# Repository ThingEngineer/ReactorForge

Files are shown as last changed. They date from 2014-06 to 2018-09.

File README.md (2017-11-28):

ReactorForge - They catalyst for creation
============

This repository contains hardware designs, board schematics, firmware, and software for ReactorForge, an open source high power induction heater platform.

Updates, polls, etc. on this project are being posted on the new Patreon page: [ReactorForge on Patreon](https://www.patreon.com/ReactorForge). You can also support the future of this project there as well.

For project status, official blog, and information about hardware availability visit [ReactorForge.com](https://reactorforge.com/) and be sure to read the [ReactorForge Wiki](https://github.com/joshcam/ReactorForge/wiki).

ReactorForge Control Board - ReactorCore
(photo: assembly of the beta ReactorCore, ReactorForge CriticalMass control board)

principal author: Joshua Campbell josh.lee.campbell@gmail.com

## Project Description
The ReactorForge project is an open source hardware platform for high power induction heating, designed for heavy use and reliable performance in real world applications.

Using fewer discreet components than most commercial induction heaters, the ReactorForge has less failure points and is easy to assemble. It is an open source project with all plans, schematics and code available under the creative commons BY-SA 4.0 license. This not only benefits the maker community and improves future designs but also makes self repair a possibility for those who have purchased kits, rather than relying on expensive factory repairs to proprietary commercial units.

The ReactorForge will be made available in a raw kit form and an ARU (Almost Ready to Use) kit that can be assembled in just a couple hours. Learn about high power electronics while building an awesome machine. The same systems in an induction heater also drive many of todays modern advances such as electric vehicles, renewable energy power inverters, cutting edge research equipment, and much more. Whether your goals are academic or you want to start using an induction heater today the ReactorForge project brings that within reach.

The ReactorForge costs thousands less than equivalent commercial models with features that are not available anywhere else. It has an easy one button/pedal interface for those that want simple to use set and forget type operation. But for those that want full control there are powerful features that let you monitor and regulate operation based on virtually any parameter. And since the entire platform is open source you have a head start to hacking the core (main control board).

CriticalMass Test Run (http://www.youtube.com/watch?v=C8s0zIcqVfk)

(video: Test run of the ReactorForge : CriticalMass +15Kw platform)

## Safety Notice and Disclaimer
An induction heater is a high power device that should be treated with hazards similar but not limited to that of induction cooktops and welders. In addition to that, the following safety guidelines should be observed:

* Don't wear metal jewelry, especially rings near the work coil. Heating can occur a few inches from the coil depending on its geometry.
* Be cautious if you have metal implants, they too could heat up if held near the work coil.
* If you have a pacemaker or other medical implants never use or be near this machine while it is in operation.
* Keep electronics at least 12 inches from the work coil while in operation to avoid damage to these devices.
* Never touch the work coil. Although it is isolated from dangerous mains current, there is still high power present. Holding metal objects that touch or short out the work coil will not harm the unit.
* Wear appropriate PPE, including but not limited to safety glasses and gloves.

We hold no responsibility or liability for injury to person or damage to property should you choose to build and operate one of these machines. If you feel you are not qualified to build or operate an induction heater find someone qualified and willing to assist you.

## Open Source
  <br />This work is licensed under a <a rel="license" href="http://creativecommons.org/licenses/by-sa/4.0/">Creative Commons Attribution-ShareAlike 4.0 International License</a>.

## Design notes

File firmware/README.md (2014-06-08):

ReactorForge Core (the main controller board) firmware is written in C. The projects presented here will use AVR Studio 6. 

Firmware can be updated with an ICSP programer via the on board programing header or by putting the unit in DFU (Device Firmware Update) mode and uploading the new firmware image over a serial connection.

Some older revisions were written in basic using the MCS Electronics BASCOM-AVR compiler, those versions are not supported or active.

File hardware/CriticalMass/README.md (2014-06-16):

ReactorForge - CriticalMass
============

CriticalMass is the general purpose base unit. Built to run on 240V single phase and be usable on a practical level with large work pieces.

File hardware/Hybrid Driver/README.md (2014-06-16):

ReactorForge - Hybrid Driver
============

This directory contains the schematic and board file for Hybrid Driver, a dual IGBT module gate driver based on the Powerex M57962L hybrid IC.

See the Wiki for [Documentation](https://github.com/joshcam/ReactorForge/wiki/ReactorForge-Hybrid-Driver)

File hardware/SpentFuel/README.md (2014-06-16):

ReactorForge - SpentFuel
============

SpentFuel is where the older prototypes that have provided a foundation for other models, learning experice and or headaches are stored. Proceed with caution!

Schematic and board designs are in CadSoft EAGLE PCB Design Software.

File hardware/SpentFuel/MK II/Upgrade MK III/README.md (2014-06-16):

MKIII - Core Upgrade
============

This was an upgrade to the prototype (MKII) using the old tank voltage feedback, PLL style control with gate drive transformer driven IGBTs. The upgrade (an early version ultimately meant to control the MKIII model) allowed the unit to run on inverter current feedback with no PLL (all digital phase control performed by the microcontroller) and make use of the new hybrid ic driver with over current protection.

The original source files for this quick upgrade were mistakenly overwritten when work on the actual Core began, all that remained was a mostly complete image export.

**Bare MKIII Control Board**

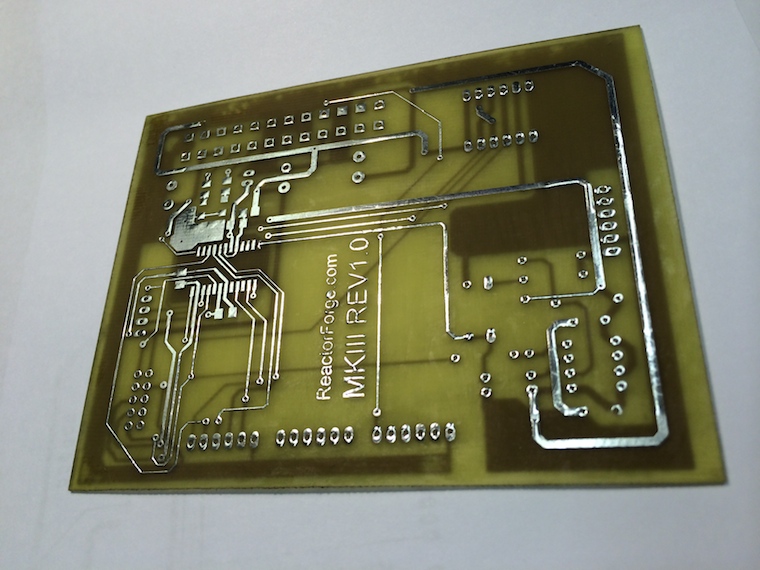
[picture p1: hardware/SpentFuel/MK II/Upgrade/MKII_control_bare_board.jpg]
Bare MKIII Control Board


**Populated MKIII Control Board**

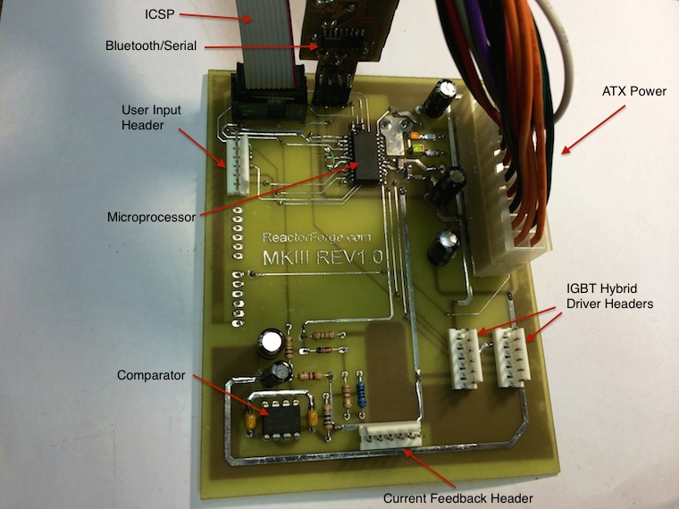
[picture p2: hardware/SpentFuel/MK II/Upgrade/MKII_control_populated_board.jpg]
Populated MKIII Control Board


**Test Run**

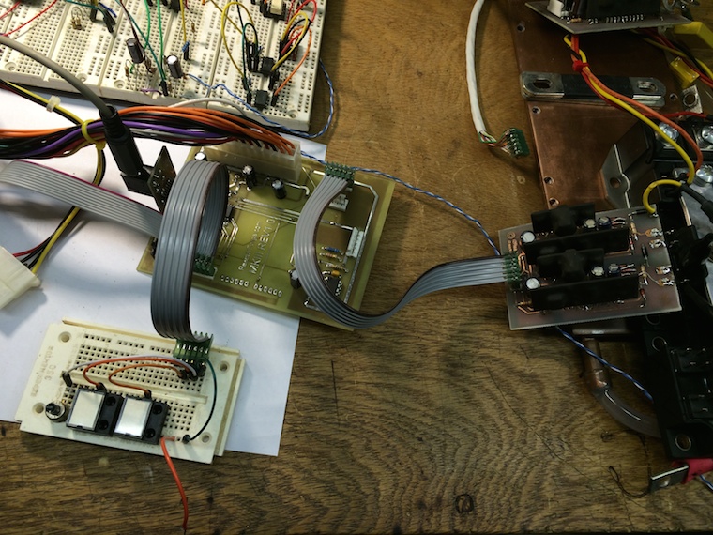
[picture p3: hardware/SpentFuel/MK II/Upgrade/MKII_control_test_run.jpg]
Test Run


**Ready To Go**

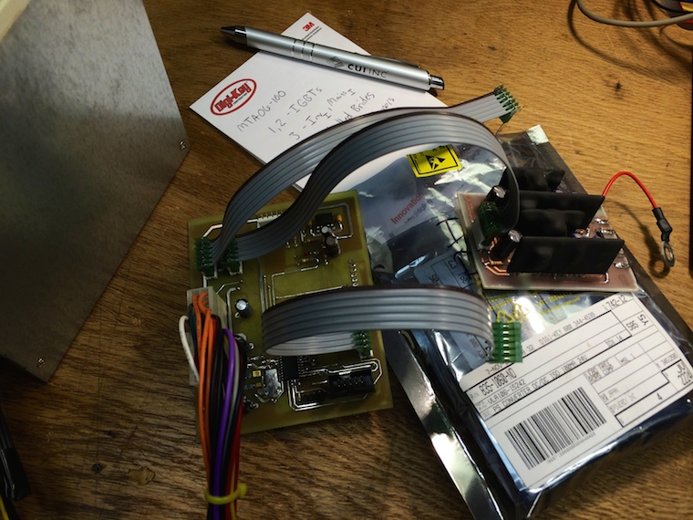
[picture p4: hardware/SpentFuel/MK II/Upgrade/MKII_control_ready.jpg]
Ready To Go


**Old MKII Board Under New MKIII Control Board**

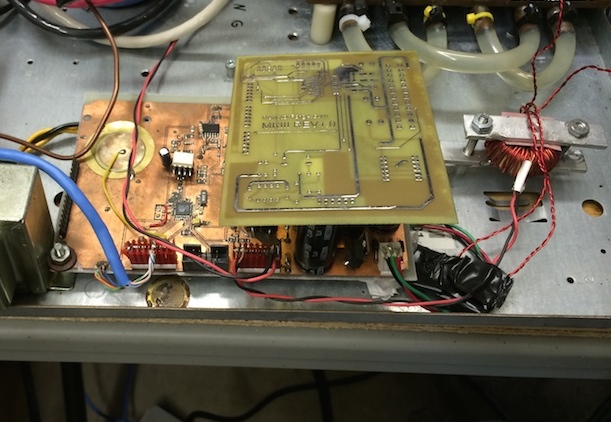
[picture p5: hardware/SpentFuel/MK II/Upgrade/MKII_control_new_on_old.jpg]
Old MKII Board Under New MKIII Control Board


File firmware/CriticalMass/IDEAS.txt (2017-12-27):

****IDEA Scratchpad****

Use a boot loader
	One port to program and monitor serial data
  Additional programmer not needed
	Will have to add a usb to serial chip and passives to main board
  Will make firmware updates / hacking easier for end user

Use an LCD with as serial backpack (i2s, spi, etc)
  Current LCD configuration uses 6 ports
  Will free up ports using a common bus
  Don't currently need the ports but its something to consider
	Simpler programing interface with standard libraries
  Slower refresh but that shouldn't matter

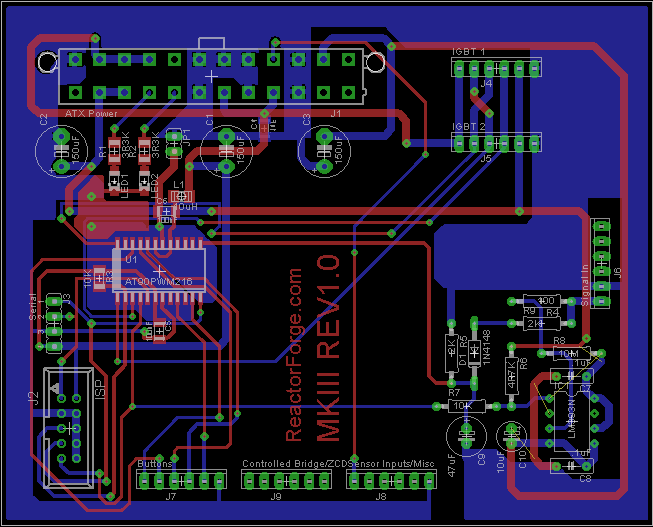
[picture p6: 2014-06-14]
hardware/SpentFuel/MK II/Upgrade MK III/MK_III_control_upgrade.png

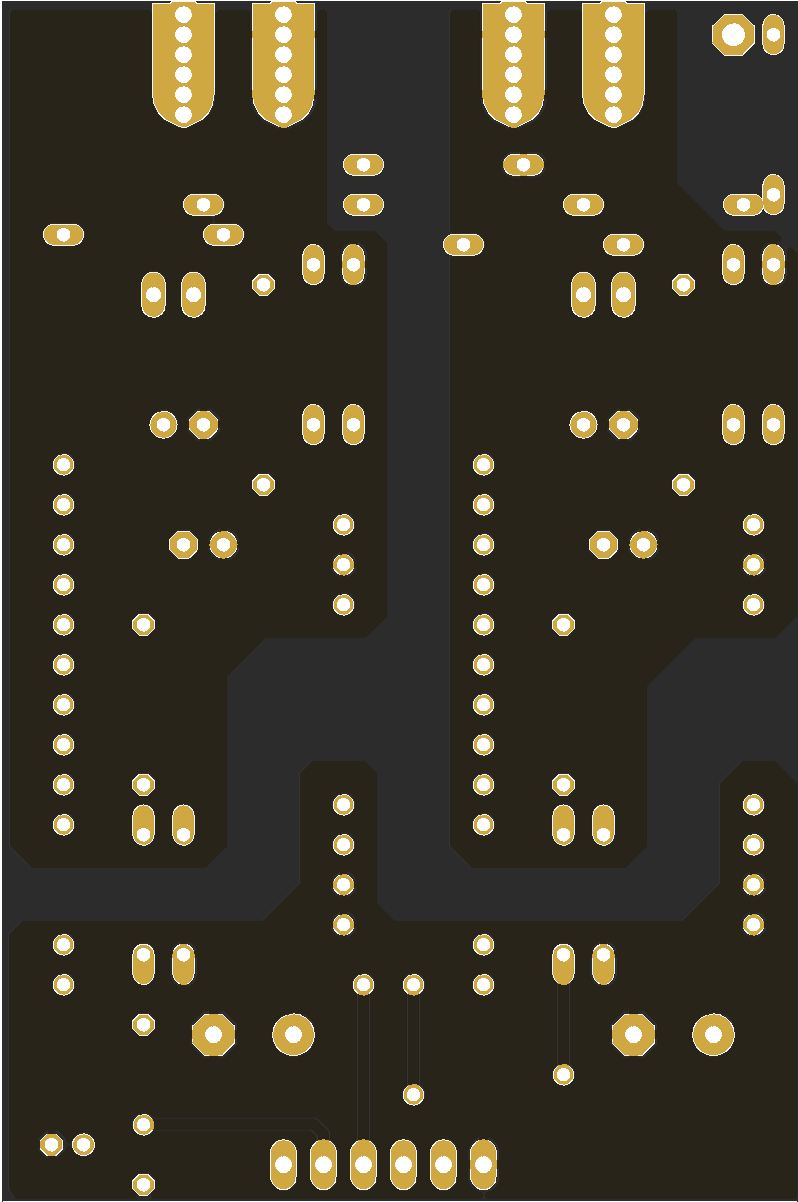
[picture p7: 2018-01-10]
hardware/Hybrid Driver/Hybrid Driver_Bottom.png

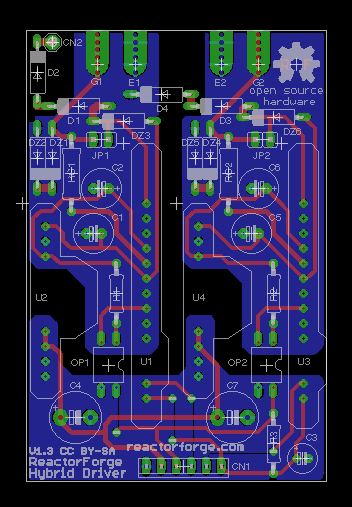
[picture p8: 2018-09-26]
hardware/Hybrid Driver/Hybrid Driver v1.3 Board.png

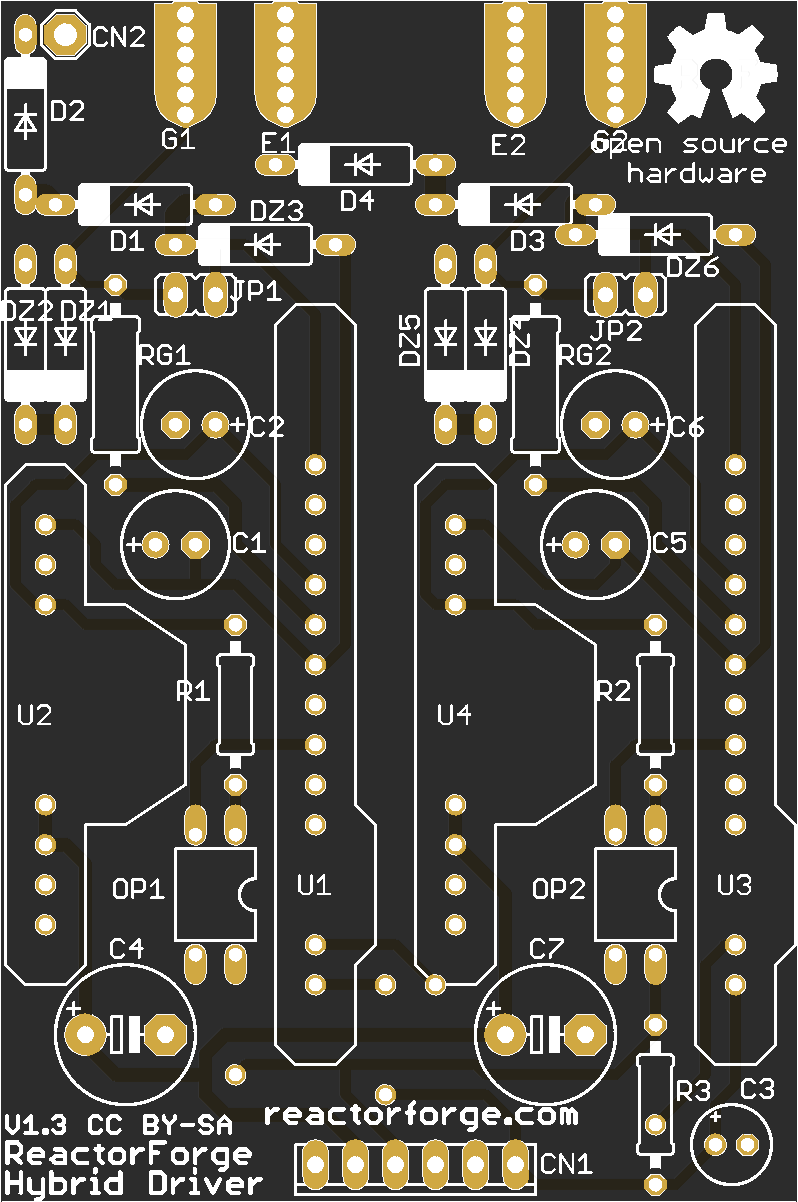
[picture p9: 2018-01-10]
hardware/Hybrid Driver/Hybrid Driver_Top.png

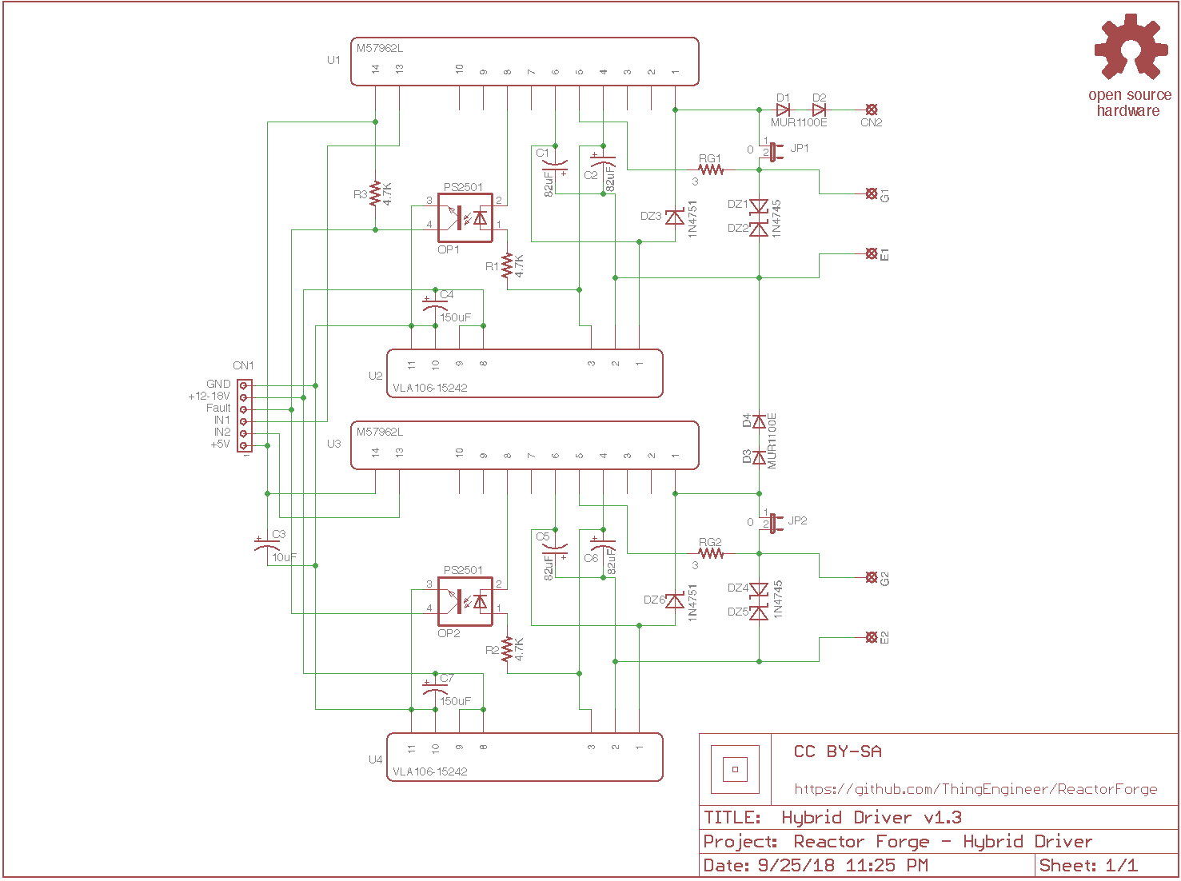
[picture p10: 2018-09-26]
hardware/Hybrid Driver/Hybrid Driver v1.3 Schematic.png

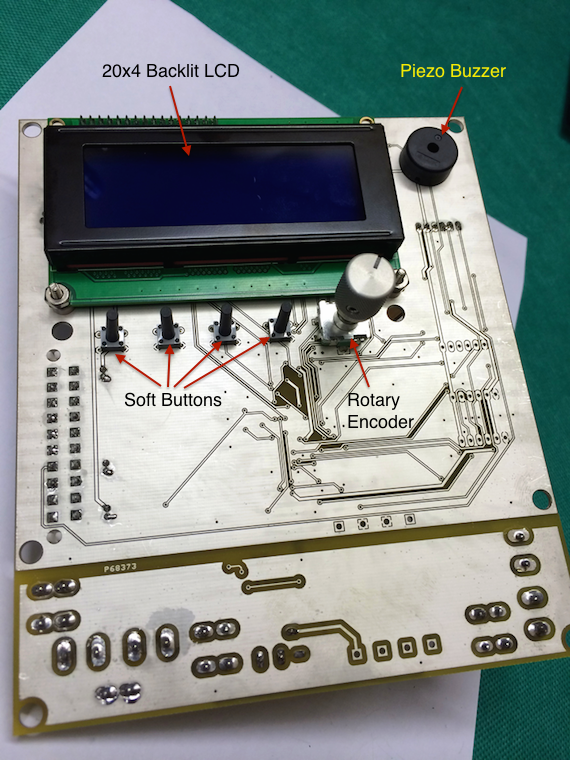
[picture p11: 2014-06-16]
doc/images/core/rf_core_front.png

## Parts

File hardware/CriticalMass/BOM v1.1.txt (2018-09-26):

Partlist exported from /Users/Josh/Dropbox/Projects/eagle/Induction Heaters/CriticalMass/Reactor Core.sch at 9/25/18 8:56 PM

Part  Value         Device                   Package                  Description                                       MF                        MPN                OC_FARNELL OC_NEWARK PN_DIGI-KEY          
C1    100uF         CPOL-USE2-5              E2-5                     POLARIZED CAPACITOR, American symbol                                                                                                     
C2    100uF         CPOL-USE2-5              E2-5                     POLARIZED CAPACITOR, American symbol                                                                                                     
C3    100uF         CPOL-USE2-5              E2-5                     POLARIZED CAPACITOR, American symbol                                                                                                     
C4    .01uF         C-USC1206                C1206                    CAPACITOR, American symbol                                                                                                               
C5    .1uF          C-USC1206K               C1206K                   CAPACITOR, American symbol                                                                                                               
C6    .1uF          C-USC1206K               C1206K                   CAPACITOR, American symbol                                                                                                               
C7    .1uF          C-USC1206                C1206                    CAPACITOR, American symbol                                                                                                               
C8    .1uF          C-USC1206                C1206                    CAPACITOR, American symbol                                                                                                               
C9    10uF          CPOL-US153CLV-0405       153CLV-0405              POLARIZED CAPACITOR, American symbol                                                                                                     
C10   .01uF         C-USC1206K               C1206K                   CAPACITOR, American symbol                                                                                                               
C11   .1uF          C-USC1206                C1206                    CAPACITOR, American symbol                                                                                                               
C12   .01uF         C-USC1206K               C1206K                   CAPACITOR, American symbol                                                                                                               
C13   .01uF         C-USC1206K               C1206K                   CAPACITOR, American symbol                                                                                                               
C14   10uF          CPOL-US153CLV-0405       153CLV-0405              POLARIZED CAPACITOR, American symbol                                                                                                     
C15   1000pF        C-USC1206                C1206                    CAPACITOR, American symbol                                                                                                               
C16   47uF          CPOL-US153CLV-0605       153CLV-0605              POLARIZED CAPACITOR, American symbol                                                                                                     
D1    NSR0340HT1G   NSR0340HT1G              SOD-323                  NSR0340HT1G                                                                                                                              
D2    1N4148        1N4148                   SOD-123                  1N4148                                                                                                                                   
D3    NSR0340HT1G   NSR0340HT1G              SOD-323                  NSR0340HT1G                                                                                                                              
D4    NSR0340HT1G   NSR0340HT1G              SOD-323                  NSR0340HT1G                                                                                                                              
D5    NSR0340HT1G   NSR0340HT1G              SOD-323                  NSR0340HT1G                                                                                                                              
D6    NSR0340HT1G   NSR0340HT1G              SOD-323                  NSR0340HT1G                                                                                                                              
D7    1N4148        1N4148                   SOD-123                  1N4148                                                                                                                                   
D8    1N4148        1N4148                   SOD-123                  1N4148                                                                                                                                   
D9    1N4148        1N4148                   SOD-123                  1N4148                                                                                                                                   
D10   1N4148        1N4148                   SOD-123                  1N4148                                                                                                                                   
D11   1N4148        1N4148                   SOD-123                  1N4148                                                                                                                                   
D16   5.1V          MM3Z5V1ST1G              SOD-323                  MM3Z5V1ST1G                                       5.1V 200MW                MM3Z5V1ST1G                             MM3Z5V1ST1GOSCT-ND   
F1    50mA Fast     TR5                      TR5                      FUSE                                              Bel Fuse Inc              MRF 50             unknown    unknown   507-1715-ND          
F2    1A Slow       FC211-5X20               FC211-5X20               FC 211                                                                                                                                   
F3    10A Slow      FC211-5X20               FC211-5X20               FC 211                                                                                                                                   
J1    ATX Power     5566-20                  5566-20                  Mini FIT connector 20 pol                                                   39-29-9206         unknown    unknown   2M3873-ND            
J2    ICSP          057-006-1                057-006-1                CONNECTOR                                                                                      unknown    unknown                        
J3    1286-ST       PIN262409-1              62409-1                  Flachstecker Typ Tyco/Electronics/AMP TAB, FASTON                                              unknown    unknown                        
J4    IGBT 1        MTA06-100                10X06MTA                 AMP connector                                                                                                                            
J5    IGBT 2        MTA06-100                10X06MTA                 AMP connector                                                                                                                            
J6    Signal In     MTA06-100                10X06MTA                 AMP connector                                                                                                                            
J7    I/O           MTA06-100                10X06MTA                 AMP connector                                                                                                                            
J8    1286-ST       PIN262409-1              62409-1                  Flachstecker Typ Tyco/Electronics/AMP TAB, FASTON                                              unknown    unknown                        
J9    1286-ST       PIN262409-1              62409-1                  Flachstecker Typ Tyco/Electronics/AMP TAB, FASTON                                              unknown    unknown                        
J10   Misc          MTA06-100                10X06MTA                 AMP connector                                                                                                                            
J11   1286-ST       PIN262409-1              62409-1                  Flachstecker Typ Tyco/Electronics/AMP TAB, FASTON                                              unknown    unknown                        
J12   1286-ST       PIN262409-1              62409-1                  Flachstecker Typ Tyco/Electronics/AMP TAB, FASTON                                              unknown    unknown                        
J13   1286-ST       PIN262409-1              62409-1                  Flachstecker Typ Tyco/Electronics/AMP TAB, FASTON                                              unknown    unknown                        
J14   1286-ST       PIN262409-1              62409-1                  Flachstecker Typ Tyco/Electronics/AMP TAB, FASTON                                              unknown    unknown                        
L1    10uH          L-USL3225P               L3225P                   INDUCTOR, American symbol                                                                                                                
L2    22uH          L-USL3225P               L3225P                   INDUCTOR, American symbol                                                                                                                
LCD1  J204A         J204A                    LCD-20X4                 J204A                                                                                                                                    
LED2                LEDCHIPLED_1206          CHIPLED_1206             LED                                                                                                                                      
LOGO1 LOGO_CC-BY-SA LOGO_CC-BY-SA            LOGO_CC-BY-SA                                                                                                                                                     
OK1   LTV816S       LTV816S                  SMD4                     OPTO COUPLER                                                                                   unknown    unknown                        
OK2   MOC3022S      MOC3022S                 6-SMD                    MOC3022S                                          Lite-On Inc               MOC3022S                                160-1377-5-ND        
OK3   MOC3022S      MOC3022S                 6-SMD                    MOC3022S                                          Lite-On Inc               MOC3022S                                160-1377-5-ND        
Q1    MMBT4401      MMBT4401                 SOT23                    MMBT4401                                                                                                                                 
Q2    MMBT4401      MMBT4401                 SOT23                    MMBT4401                                                                                                                                 
Q4    MMBT4401      MMBT4401                 SOT23                    MMBT4401                                                                                                                                 
R1    1K            R-US_R1206               R1206                    RESISTOR, American symbol                         Stackpole Electronics Inc RNCP1206FTD100R                         RNCP1206FTD100RCT-ND 
R2    220           R-US_R1206               R1206                    RESISTOR, American symbol                                                                                                                
R3    10K           R-US_R1206               R1206                    RESISTOR, American symbol                                                                                                                
R4    100           R-US_R1206               R1206                    RESISTOR, American symbol                                                                                                                
R5    4K7           R-US_R1206               R1206                    RESISTOR, American symbol                                                                                                                
R6    4K7           R-US_R1206               R1206                    RESISTOR, American symbol                                                                                                                
R7    10K           R-US_R1206               R1206                    RESISTOR, American symbol                                                                                                                
R8    10M           R-US_R1206               R1206                    RESISTOR, American symbol                                                                                                                
R9    100           R-US_R1206               R1206                    RESISTOR, American symbol                                                                                                                
R10   330           R-US_M1206               M1206                    RESISTOR, American symbol                                                                                                                
R12   330           R-US_R1206               R1206                    RESISTOR, American symbol                                                                                                                
R13   220K          R-US_R1206               R1206                    RESISTOR, American symbol                                                                                                                
R14   10K           R-US_R1206               R1206                    RESISTOR, American symbol                                                                                                                
R16   10K           TRIMMER_3314G            TRIMMER_3314G            3314G Trimmer Pot                                                                                                                        
R17   2k            R-US_R1206               R1206                    RESISTOR, American symbol                                                                                                                
R18   330R          R-US_R1206               R1206                    RESISTOR, American symbol                                                                                                                
R19   620R          R-US_R1206               R1206                    RESISTOR, American symbol                                                                                                                
R20   1K            R-US_R1206               R1206                    RESISTOR, American symbol                                                                                                                
R21   3K3           R-US_R1206               R1206                    RESISTOR, American symbol                                                                                                                
R22   1K            R-US_R1206               R1206                    RESISTOR, American symbol                                                                                                                
R23   100R          R-US_R1206               R1206                    RESISTOR, American symbol                                                                                                                
R24   4K7           R-US_R1206               R1206                    RESISTOR, American symbol                                                                                                                
R25   10K           R-US_M1206               M1206                    RESISTOR, American symbol                                                                                                                
R26   10K           R-US_M1206               M1206                    RESISTOR, American symbol                                                                                                                
R27   10K           R-US_R1206               R1206                    RESISTOR, American symbol                                                                                                                
R28   10K           R-US_R1206               R1206                    RESISTOR, American symbol                                                                                                                
R29   1K            R-US_R1206               R1206                    RESISTOR, American symbol                                                                                                                
R30   220K          R-US_R1206               R1206                    RESISTOR, American symbol                                                                                                                
R31   22K           R-US_R1206               R1206                    RESISTOR, American symbol                                                                                                                
R32   1K            R-US_R1206               R1206                    RESISTOR, American symbol                                                                                                                
R33   4K7           R-US_R1206               R1206                    RESISTOR, American symbol                                                                                                                
R34   100           R-US_R1206               R1206                    RESISTOR, American symbol                         Stackpole Electronics Inc RNCP1206FTD100R                         RNCP1206FTD100RCT-ND 
R35   24            R-US_R2512               R2512                    RESISTOR, American symbol                         TE Connectivity           352124RFT                               A115993CT-ND         
R36   330           R-US_R1206               R1206                    RESISTOR, American symbol                                                                                                                
R37   330           R-US_R1206               R1206                    RESISTOR, American symbol                                                                                                                
R38   2K            R-US_R1206               R1206                    RESISTOR, American symbol                         Stackpole Electronics Inc RNCP1206FTD100R                         RNCP1206FTD100RCT-ND 
R39   330           R-US_R1206               R1206                    RESISTOR, American symbol                                                                                                                
SG1   PS1740P02E    F/EE17P                  F/EE17P                  BUZZER Source: Buerklin                                                     PS1740P02E         unknown    unknown   445-2528-ND          
SJ1   0             SJ                       SJ                       SMD solder JUMPER                                                                                                                        
SJ2   0             SJ                       SJ                       SMD solder JUMPER                                                                                                                        
SW1   PEC11R_SW     PEC11R_SW                BOURNS_PEC11R_SW         Bourns Rotary Encoder PEC11R series with switch   Bourns                    PEC11R-4215K-S0012                      PEC11R-4215K-S0012-ND
SW2   FSM14JH       SW_TACTILE_TOP_ACTIVATED SW_TACTILE_TOP_ACTIVATED                                                                                                                                          
SW3   FSM14JH       SW_TACTILE_TOP_ACTIVATED SW_TACTILE_TOP_ACTIVATED                                                                                                                                          
SW4   FSM14JH       SW_TACTILE_TOP_ACTIVATED SW_TACTILE_TOP_ACTIVATED                                                                                                                                          
SW5   FSM14JH       SW_TACTILE_TOP_ACTIVATED SW_TACTILE_TOP_ACTIVATED                                                                                                                                          
T1    4A            T435-600B-TR             DPAK-TRIAC               T435-600B-TR                                      STMicroelectronics        T435-600B-TR                            497-2513-1-ND        
T2    16A           T435-600B-TR             DPAK-TRIAC               T435-600B-TR                                      STMicroelectronics        T1635-700G-TR                           497-4433-1-ND        
U1    AT90PWM316    AT90PWM316               SOIC-32                                                                                                                                                           
U3    LM393M        LM393D                   SO08                     COMPARATOR                                        Fairchild Semiconductor   LM393M                                  LM393MFS-ND          
X1    FS10-110-C2   FS10-110-C2              FS10-110-C2              FS10-110-C2                                       Triad Magnetics           FS10-110-C2-B                           237-1578-ND

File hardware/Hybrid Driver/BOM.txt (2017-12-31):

Partlist

Exported from Hybrid Driver.brd at 12/30/17 5:46 PM

EAGLE Version 8.5.1 Copyright (c) 1988-2017 Autodesk, Inc.

Assembly variant: 

Part     Value          Package                    Library     Position (inch)       Orientation

C1       82uF           E2,5-7                     resistor    (0.45 1.65)           R0
C2       82uF           E2,5-7                     resistor    (0.5 1.95)            R180
C3       10uF           E2-5                       rcl         (1.84 0.15)           R0
C4       150uF          E5-8,5                     resistor    (0.325 0.425)         R0
C5       82uF           E2,5-7                     resistor    (1.5 1.65)            R0
C6       82uF           E2,5-7                     resistor    (1.55 1.95)           R180
C7       150uF          E5-8,5                     resistor    (1.375 0.425)         R0
CN1      MTA100-6       10X06MTA                   con-amp     (1.05 0.1)            R180
CN2      SE14           SE14                       solpad      (0.175 2.925)         R0
D1       MUR1100E       DO07                       diode       (0.35 2.5)            R0
D2       MUR1100E       DO07                       diode       (0.075 2.725)         R270
D3       MUR1100E       DO07                       diode       (1.3 2.5)             R0
D4       MUR1100E       DO07                       diode       (0.9 2.6)             R0
DZ1      1N4745         DIODE.4-AXIAL              1-Custom    (0.175 2.15)          R90
DZ2      1N4745         DIODE.4-AXIAL              1-Custom    (0.075 2.15)          R90
DZ3      1N4751         DIODE.4-AXIAL              1-Custom    (0.65 2.4)            R0
DZ4      1N4745         DIODE.4-AXIAL              1-Custom    (1.225 2.15)          R90
DZ5      1N4745         DIODE.4-AXIAL              1-Custom    (1.125 2.15)          R90
DZ6      1N4751         DIODE.4-AXIAL              1-Custom    (1.65 2.425)          R0
E1       IGBT-PAD       IGBT-PAD                   1-Custom    (0.725 2.775)         R0
E2       IGBT-PAD       IGBT-PAD                   1-Custom    (1.3 2.775)           R0
G1       IGBT-PAD       IGBT-PAD                   1-Custom    (0.475 2.775)         R0
G2       IGBT-PAD       IGBT-PAD                   1-Custom    (1.55 2.775)          R0
JP1      0              JP1                        jumper      (0.5 2.275)           R90
JP2      0              JP1                        jumper      (1.575 2.275)         R90
OP1      PS2501         DIL04                      optocoupler (0.55 0.775)          R180
OP2      PS2501         DIL04                      optocoupler (1.6 0.775)           R180
R1       4.7K           0207/10                    resistor    (0.6 1.25)            R270
R2       4.7K           0207/10                    resistor    (1.65 1.25)           R270
R3       4.7K           0207/10                    resistor    (1.65 0.25)           R270
RG1      3              0309/12                    resistor    (0.3 2.05)            R90
RG2      3              0309/12                    resistor    (1.35 2.05)           R90
U1       M57962L        HYBRID-IC-IBGT-GATE-DRIVER 1-Custom    (0.65 2.25)           R270
U2       VLA106-15242   ISOLATED_DC_DC_CONVERTER   1-Custom    (-0.025 1.85)         R270
U3       M57962L        HYBRID-IC-IBGT-GATE-DRIVER 1-Custom    (1.7 2.25)            R270
U4       VLA106-15242   ISOLATED_DC_DC_CONVERTER   1-Custom    (1 1.85)              R270

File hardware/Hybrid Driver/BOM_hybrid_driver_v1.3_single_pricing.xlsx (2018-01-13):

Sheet: Digi-Key
Index | Quantity | Digi-Key Part Number | Manufacturer Part Number | Manufacturer | Description | Unit Price USD | Extended Price USD
1 | 2 | MUR1100EGOS-ND (https://www.digikey.com/scripts/DkSearch/dksus.dll?Detail&itemSeq=248809026&uq=636513504784148564) | MUR1100EG | ON Semiconductor | DIODE GEN PURP 1KV 1A AXIAL | $0.52 | $1.04
2 | 4 | 1N4745AFSCT-ND (https://www.digikey.com/scripts/DkSearch/dksus.dll?Detail&itemSeq=248809126&uq=636513504784148564) | 1N4745ATR | ON Semiconductor | DIODE ZENER 16V 1W DO41 | $0.25 | $1.00
3 | 2 | 1N4751AFSCT-ND (https://www.digikey.com/scripts/DkSearch/dksus.dll?Detail&itemSeq=248809317&uq=636513504784158566) | 1N4751ATR | ON Semiconductor | DIODE ZENER 30V 1W DO41 | $0.27 | $0.54
4 | 2 | PS2501A-1-A-ND (https://www.digikey.com/scripts/DkSearch/dksus.dll?Detail&itemSeq=248809542&uq=636513504784158566) | PS2501A-1-A | CEL | OPTOISOLATOR 5KV TRANS 4DIP | $0.50 | $1.00
5 | 4 | 493-1860-ND (https://www.digikey.com/scripts/DkSearch/dksus.dll?Detail&itemSeq=248854342&uq=636513504784158566) | UPW1V820MED | Nichicon | CAP ALUM 82UF 20% 35V RADIAL | $0.35 | $1.40
6 | 2 | P10295-ND (https://www.digikey.com/scripts/DkSearch/dksus.dll?Detail&itemSeq=248855875&uq=636513504784168568) | EEU-FC1V151 | Panasonic | CAP ALUM 150UF 20% 35V RADIAL | $0.44 | $0.88
7 | 1 | 493-1767-ND (https://www.digikey.com/scripts/DkSearch/dksus.dll?Detail&itemSeq=248856906&uq=636513504784168568) | UPW1C100MDD | Nichicon | CAP ALUM 10UF 20% 16V RADIAL | $0.18 | $0.18
8 | 2 | 3.0WCT-ND (https://www.digikey.com/scripts/DkSearch/dksus.dll?Detail&itemSeq=248858464&uq=636513504784178570) | FMP100JR-52-3R | Yageo | RES 3 OHM 1W 5% AXIAL | $0.17 | $0.34
9 | 3 | 4.7KQBK-ND (https://www.digikey.com/scripts/DkSearch/dksus.dll?Detail&itemSeq=248859613&uq=636513504784178570) | CFR-25JB-52-4K7 | Yageo | RES 4.7K OHM 1/4W 5% AXIAL | $0.10 | $0.30
10 | 2 | 0.0QBK-ND (https://www.digikey.com/scripts/DkSearch/dksus.dll?Detail&itemSeq=248921997&uq=636513904509629941) | ZOR-25-B-52-0R | Yageo | 0 OHM 1/4W JUMP | $0.10 | $0.20
11 | 1 | A1923-ND (https://www.digikey.com/product-detail/en/te-connectivity-amp-connectors/640456-6/A1923-ND/109008) | 640456-6 | TE Connectivity | MTA CONN HEADER 6POS .100 TIN | $0.27 | $0.27
12 | 2 | 835-1107-ND (https://www.digikey.com/products/en?keywords=M57962L) | M57962L | Powerex | HYBRID IC IBGT GATE DRIVER | $21.74 | $43.48
13 | 2 | VLA106-15242 (https://www.digikey.com/products/en?keywords=VLA106-15242) | VLA106-15242 | Powerex | ISOLATED DC DC CONVERTER | $14.76 | $29.52
 |  |  |  |  |  | Total | $80.15
 |  | Notes
 |  | All capacitors must be low Impedance
 |  | Al capacitors should be one of the following brands: Rubycon, Nichicon Panasonic, Mallory, or Sanyo/Nippon

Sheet: Mouser
To Do

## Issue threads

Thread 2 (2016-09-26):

Kit still coming?

3DTOPO, 2016-09-26:
It looks like no changes have been pushed in 2 years. Just wondering if this project was still being developed and if kits where still going to be made available?

ThingEngineer, 2017-11-10:
Hey, despite some delay yes this project is still very much alive. I am working on getting the current version of code and schematics cleaned up and ready for release!

You can now support [ReactorForge on Patreon](http://www.patreon.com/ReactorForge), but you definitely don't have to!

Closed 2017-11-10.

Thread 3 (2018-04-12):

Repository uses arduino topic but is in no way an Arduino project

per1234, 2018-04-12:
The code is not compatible with the Arduino IDE.

The hardware does not use an Arduino board.

Therefore the use of the `arduino` topic is not appropriate. Please remove it from this repository.

ThingEngineer, 2018-04-12:
You are correct. At one point I had some parts of this project coded in Arduino and was planing on moving more to the platform but opted not to. I'll update the topics, thanks for the heads up!

Closed 2018-04-12.

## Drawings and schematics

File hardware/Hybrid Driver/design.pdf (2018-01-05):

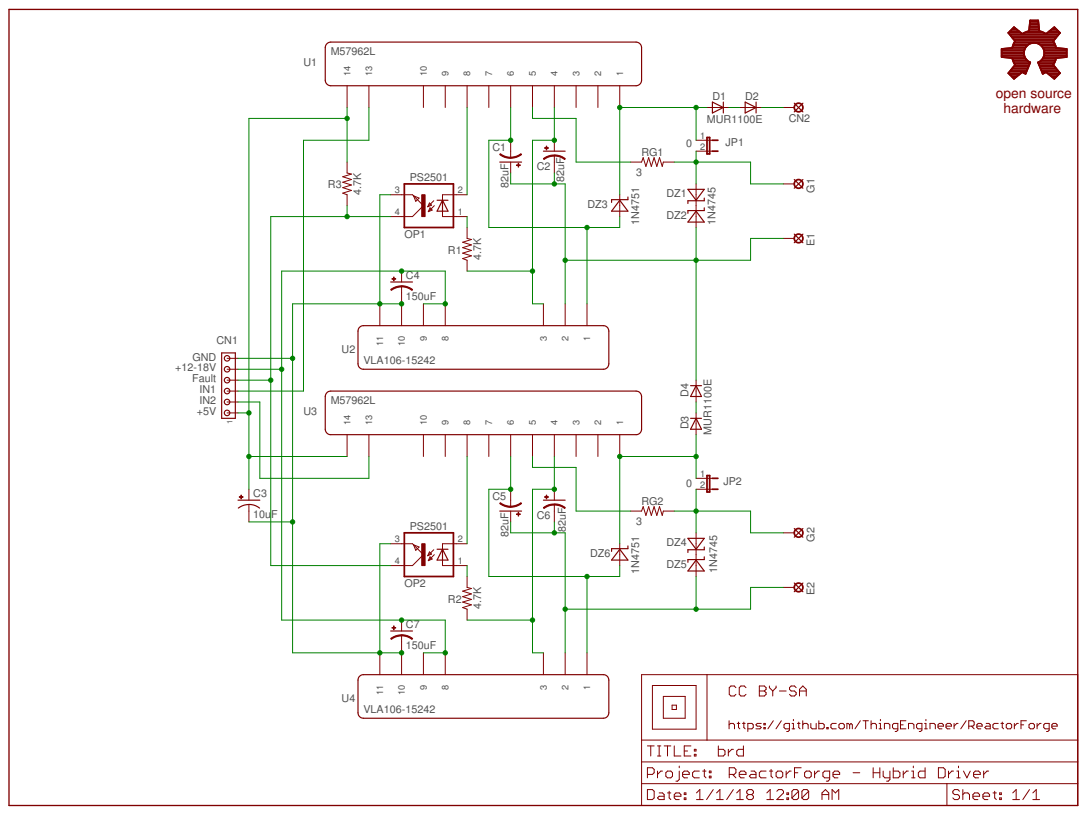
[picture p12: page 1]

CN2

D1

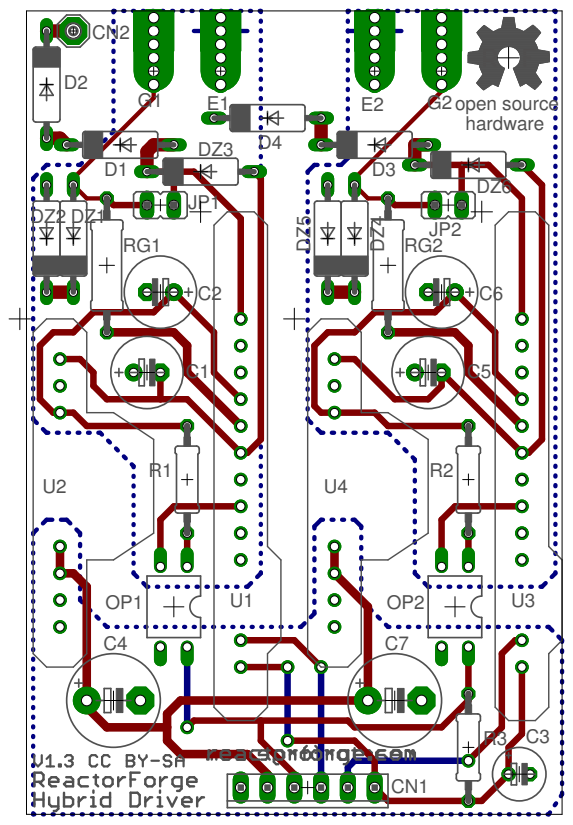
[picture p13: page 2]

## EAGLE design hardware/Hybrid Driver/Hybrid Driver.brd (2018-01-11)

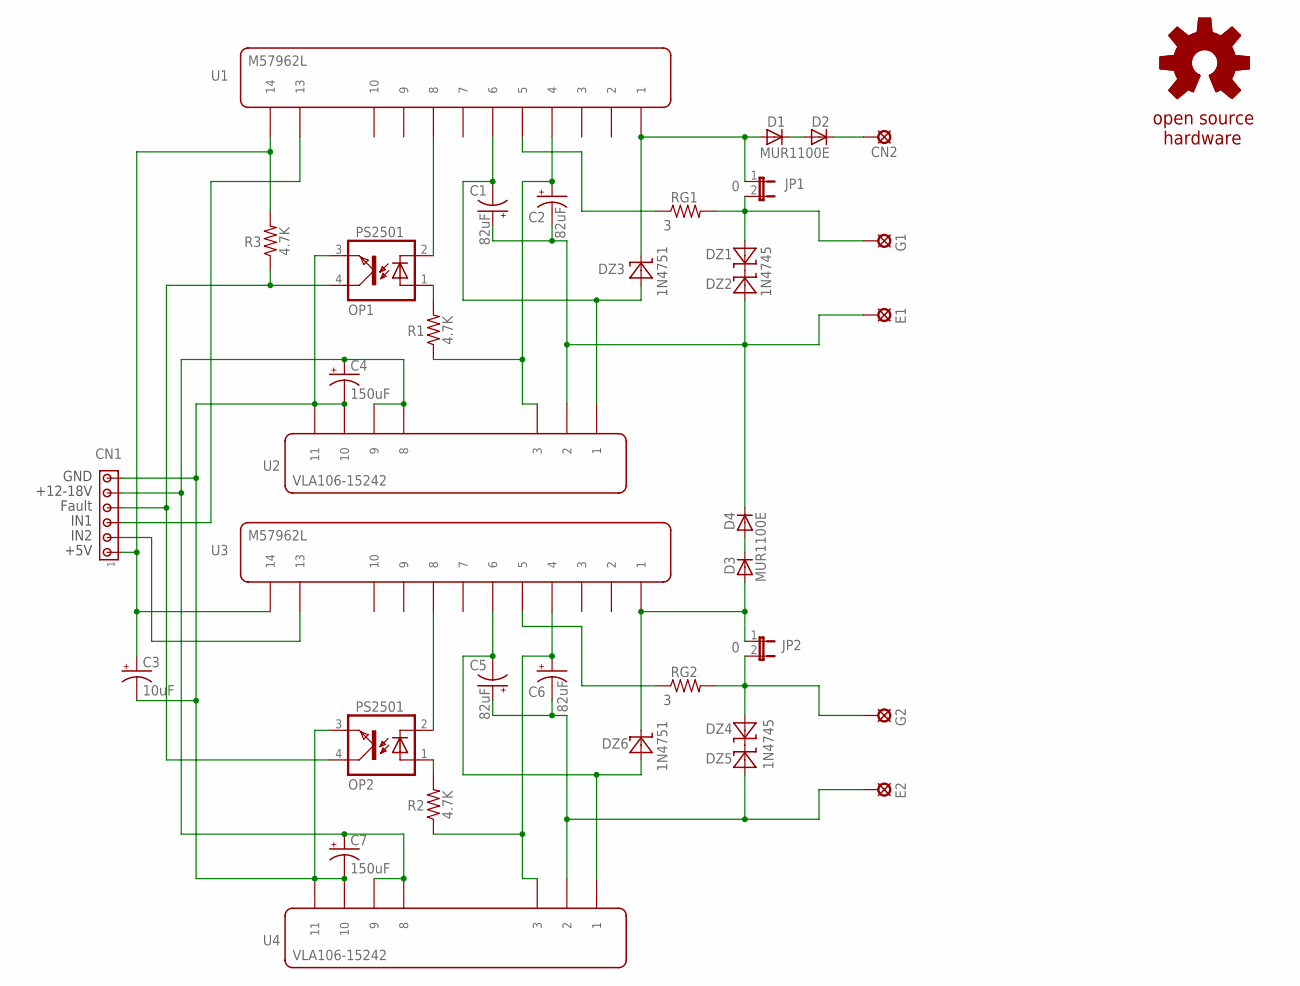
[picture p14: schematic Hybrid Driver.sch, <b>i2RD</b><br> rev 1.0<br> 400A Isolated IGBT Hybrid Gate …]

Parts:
C1, C2, C5, C6: 82uF; E2,5-7
C3: 10uF; E2-5
C4, C7: 150uF; E5-8,5
CN1: MTA100-6; 10X06MTA
CN2: SE14
D1, D2, D3, D4: MUR1100E; DO07
DZ1, DZ2, DZ4, DZ5: 1N4745; DIODE.4-AXIAL
DZ3, DZ6: 1N4751; DIODE.4-AXIAL
E1, E2: IGBT-PAD
G1, G2: IGBT-PAD
GOLD_ORB_SM1: OSHWLOGOLOGO8MM; OSHW_8MM
JP1, JP2: 0; JP1
OP1, OP2: PS2501; DIL04
R1, R2, R3: 4.7K; 0207/10
RG1, RG2: 3; 0309/12
U1, U3: M57962L; HYBRID-IC-IBGT-GATE-DRIVER
U2, U4: VLA106-15242; ISOLATED_DC_DC_CONVERTER

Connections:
G1: DZ1.A, G1.1, G1.2, G1.3, G1.4, G1.5, G1.6, JP1.2, RG1.2
G2: DZ4.A, G2.1, G2.2, G2.3, G2.4, G2.5, G2.6, JP2.2, RG2.2
GND: C3.-, C4.-, C7.-, CN1.1 (6), OP1.3 (EMIT), OP2.3 (EMIT), U2.10, U2.11, U4.10, U4.11
GND-E1: C1.+, C2.-, D4.C, DZ2.A, E1.1, E1.2, E1.3, E1.4, E1.5, E1.6, U2.2
GND-E2: C5.+, C6.-, DZ5.A, E2.1, E2.2, E2.3, E2.4, E2.5, E2.6, U4.2
unnamed: D1.C, D2.A
unnamed: CN2.MP, D2.C
unnamed: D1.A, DZ3.C, JP1.1, U1.1
unnamed: OP2.1 (A), R2.2
unnamed: DZ1.C, DZ2.C
unnamed: DZ4.C, DZ5.C
unnamed: C3.+, CN1.6 (1), R3.2, U1.14, U3.14
unnamed: OP2.2 (C), U3.8
unnamed: OP1.2 (C), U1.8
unnamed: OP1.1 (A), R1.2
unnamed: CN1.3 (4), OP1.4 (COL), OP2.4 (COL), R3.1
unnamed: C5.-, DZ6.A, U3.6, U4.1
unnamed: C1.-, DZ3.A, U1.6, U2.1
unnamed: C2.+, R1.1, U1.4, U2.3
unnamed: RG2.1, U3.5
unnamed: C6.+, R2.1, U3.4, U4.3
unnamed: RG1.1, U1.5
unnamed: D3.A, DZ6.C, JP2.1, U3.1
unnamed: D3.C, D4.A
unnamed: C4.+, C7.+, CN1.2 (5), U2.8, U2.9, U4.8, U4.9
unnamed: CN1.4 (3), U1.13
unnamed: CN1.5 (2), U3.13

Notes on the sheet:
GND
+12-18V
Fault
IN1
IN2
+5V

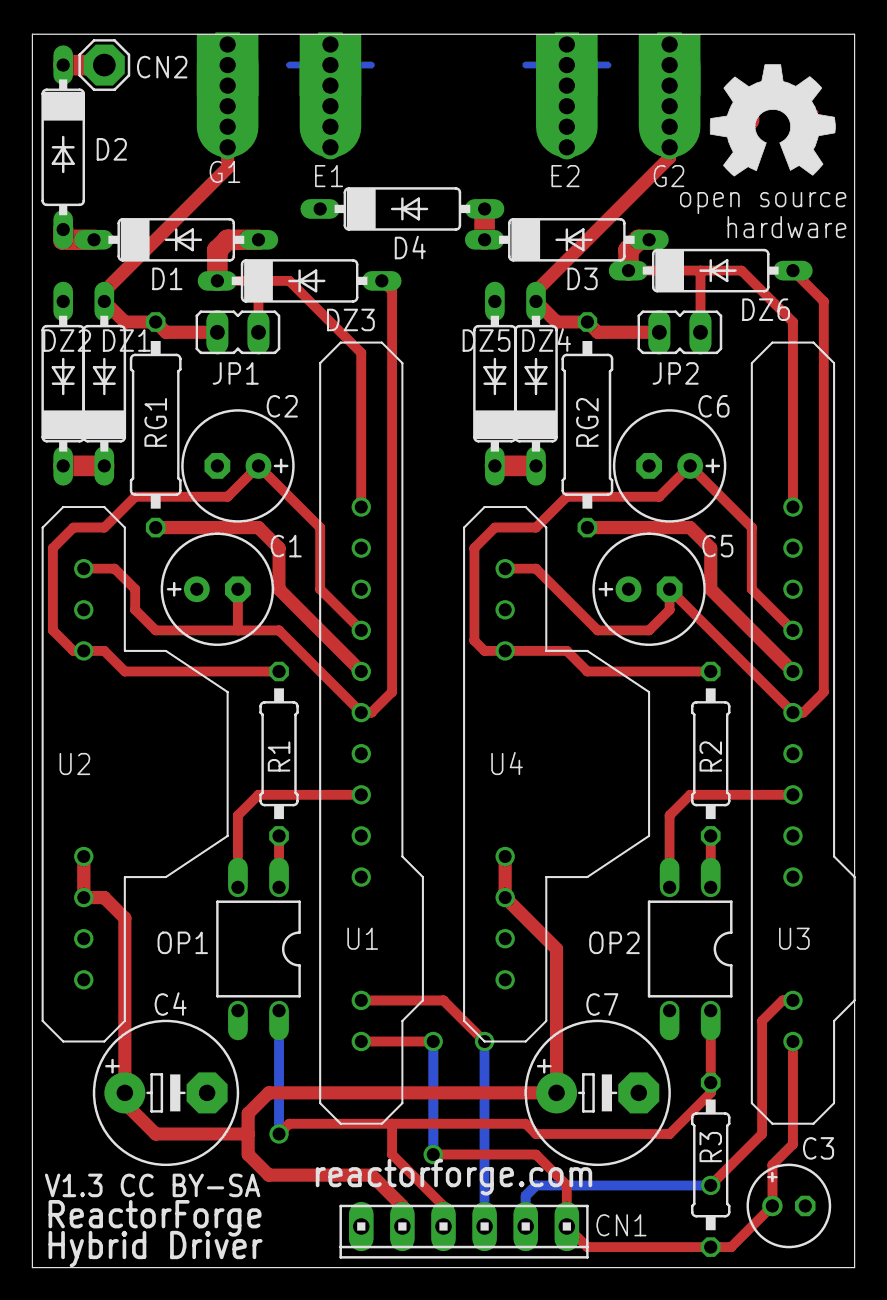
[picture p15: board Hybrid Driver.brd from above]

Board: 2 copper layers, 50.8 x 76.2 mm, 37 parts (0 on the bottom side), 27 nets.

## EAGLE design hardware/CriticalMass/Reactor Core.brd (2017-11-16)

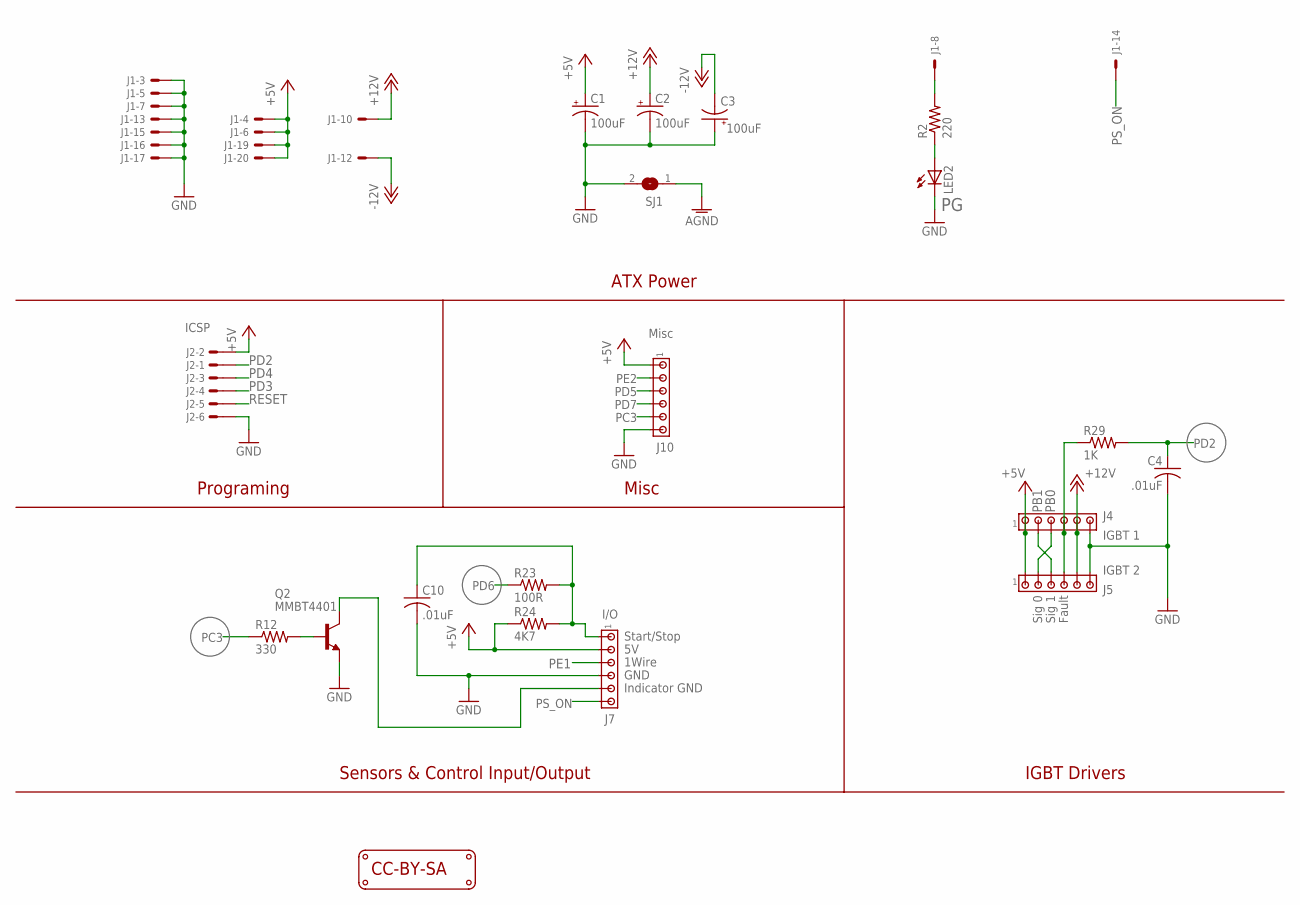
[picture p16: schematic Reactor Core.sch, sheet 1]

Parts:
C1, C2, C3: 100uF; E2-5
C4: .01uF; C1206
C10: .01uF; C1206K
J1: ATX Power; 5566-20; MPN 39-29-9206
J2: ICSP; 057-006-1
J4: IGBT 1; 10X06MTA
J5: IGBT 2; 10X06MTA
J7: I/O; 10X06MTA
J10: Misc; 10X06MTA
LED2: LEDCHIPLED_1206; CHIPLED_1206
LOGO1: LOGO_CC-BY-SA
Q2: MMBT4401; SOT23
R2: 220; R1206
R12: 330; R1206
R23: 100R; R1206
R24: 4K7; R1206
R29: 1K; R1206
SJ1: 0; SJ

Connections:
+5V: C1.+, J1.4, J1.6, J1.19, J1.20, J2.2, J4.6 (1), J5.6 (1), J7.5 (2), J10.6 (1), R24.1; also elsewhere on the board
+12V: C2.+, J1.10, J4.2 (5), J5.2 (5); also elsewhere on the board
-12V: C3.-, J1.12; also elsewhere on the board
AGND: SJ1.1; also elsewhere on the board
FAULT: J4.3 (4), J5.3 (4), R29.1
GND: C1.-, C2.-, C3.+, C4.2, C10.2, J1.3, J1.5, J1.7, J1.13, J1.15, J1.16, J1.17, J2.6, J4.1 (6), J5.1 (6), J7.3 (4), J10.1 (6), LED2.C, Q2.2 (E), SJ1.2; also elsewhere on the board
unnamed: LED2.A, R2.1
unnamed: J7.2 (5), Q2.3 (C)
unnamed: Q2.1 (B), R12.2
unnamed: C10.1, J7.6 (1), R23.2, R24.2
PB0: J4.4 (3), J5.5 (2); also elsewhere on the board
PB1: J4.5 (2), J5.4 (3); also elsewhere on the board
PC3: J10.2 (5), R12.1; also elsewhere on the board
PD2: C4.1, J2.1, R29.2; also elsewhere on the board
PD3: J2.4; also elsewhere on the board
PD4: J2.3; also elsewhere on the board
PD5: J10.4 (3); also elsewhere on the board
PD6: R23.1; also elsewhere on the board
PD7: J10.3 (4); also elsewhere on the board
PE1: J7.4 (3); also elsewhere on the board
PE2: J10.5 (2); also elsewhere on the board
PG: J1.8, R2.2
PS_ON: J1.14, J7.1 (6)
RESET: J2.5; also elsewhere on the board

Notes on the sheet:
ATX Power
Programing
Sensors & Control Input/Output
Start/Stop
1Wire
Indicator GND
Misc
GND
IGBT Drivers
Fault
Sig 1
Sig 0

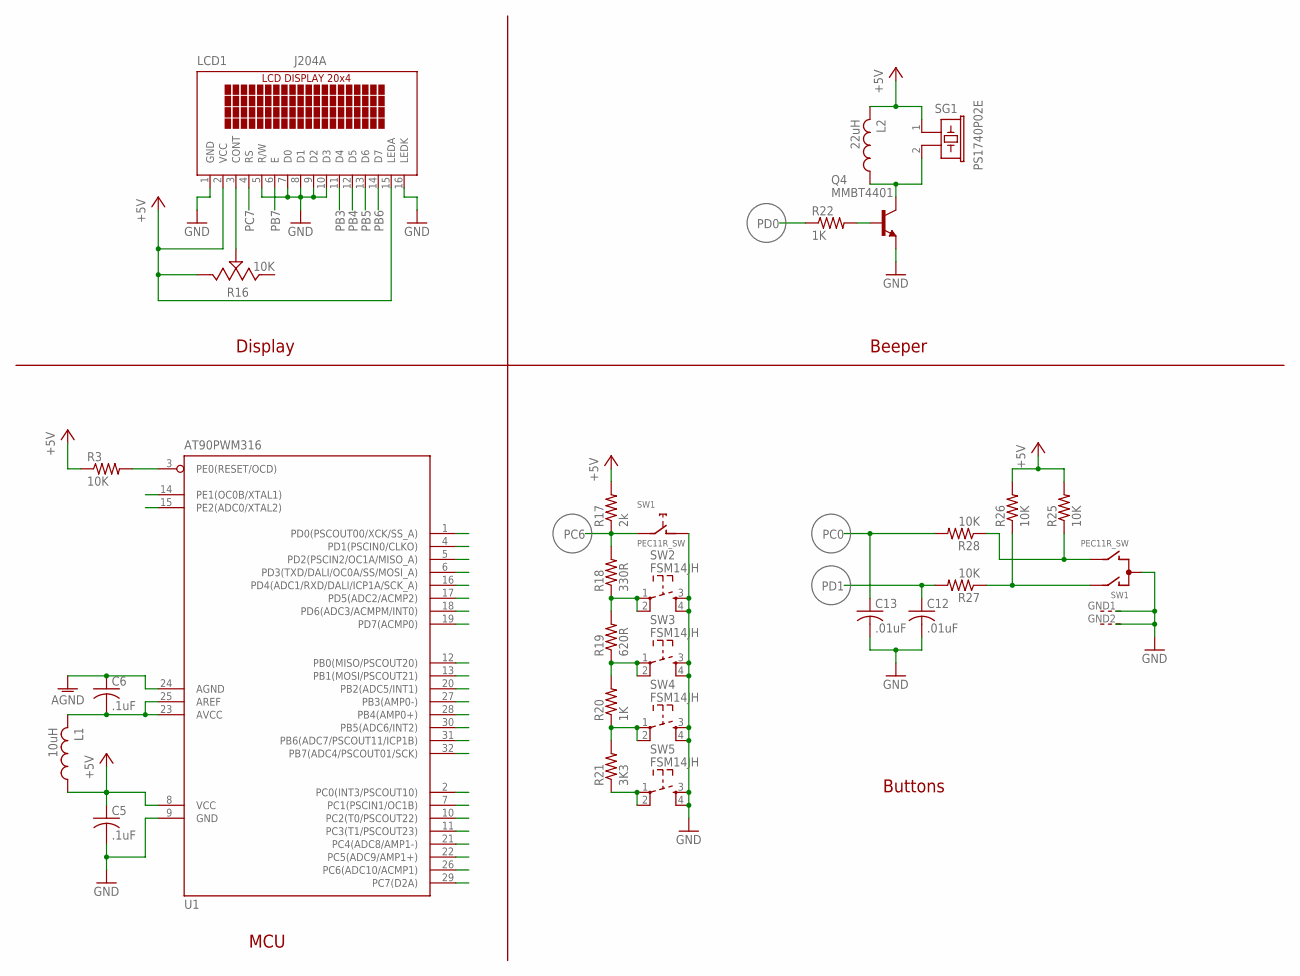
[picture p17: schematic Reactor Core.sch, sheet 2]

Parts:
C5, C6: .1uF; C1206K
C12, C13: .01uF; C1206K
L1: 10uH; L3225P
L2: 22uH; L3225P
LCD1: J204A; LCD-20X4
Q4: MMBT4401; SOT23
R3, R27, R28: 10K; R1206
R16: 10K; TRIMMER_3314G
R17: 2k; R1206
R18: 330R; R1206
R19: 620R; R1206
R20, R22: 1K; R1206
R21: 3K3; R1206
R25, R26: 10K; M1206
SG1: PS1740P02E; F/EE17P; MPN PS1740P02E
SW1: PEC11R_SW; BOURNS_PEC11R_SW
SW2, SW3, SW4, SW5: FSM14JH; SW_TACTILE_TOP_ACTIVATED
U1: AT90PWM316; SOIC-32

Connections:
+5V: C5.1, L1.1, L2.2, LCD1.2 (VCC), LCD1.15 (LEDA), R3.1, R16.3, R17.2, R25.2, R26.2, SG1.1, U1.8 (VCC); also elsewhere on the board
AGND: C6.1, U1.24 (AGND); also elsewhere on the board
AVCC: C6.2, L1.2, U1.23 (AVCC), U1.25 (AREF)
GND: C5.2, C12.2, C13.2, LCD1.1 (GND), LCD1.5 (R/W), LCD1.7 (D0), LCD1.8 (D1), LCD1.9 (D2), LCD1.10 (D3), LCD1.16 (LEDK), Q4.2 (E), SW1.C, SW1.GND1 (G), SW1.GND2 (G), SW1.S (1), SW2.3, SW2.4, SW3.3, SW3.4, SW4.3, SW4.4, SW5.3, SW5.4, U1.9 (GND); also elsewhere on the board
unnamed: LCD1.3 (CONT), R16.2
unnamed: L2.1, Q4.3 (C), SG1.2
unnamed: Q4.1 (B), R22.2
unnamed: R25.1, R28.1, SW1.B
unnamed: R26.1, R27.1, SW1.A
unnamed: R21.1, SW5.1, SW5.2
unnamed: R18.1, R19.2, SW2.1, SW2.2
unnamed: R19.1, R20.2, SW3.1, SW3.2
unnamed: R20.1, R21.2, SW4.1, SW4.2
PB0: U1.12 (PB0(MISO/PSCOUT20)); also elsewhere on the board
PB1: U1.13 (PB1(MOSI/PSCOUT21)); also elsewhere on the board
PB2: U1.20 (PB2(ADC5/INT1)); also elsewhere on the board
PB3: LCD1.11 (D4), U1.27 (PB3(AMP0-))
PB4: LCD1.12 (D5), U1.28 (PB4(AMP0+))
PB5: LCD1.13 (D6), U1.30 (PB5(ADC6/INT2))
PB6: LCD1.14 (D7), U1.31 (PB6(ADC7/PSCOUT11/ICP1B))
PB7: LCD1.6 (E), U1.32 (PB7(ADC4/PSCOUT01/SCK))
PC0: C13.1, R28.2, U1.2 (PC0(INT3/PSCOUT10))
PC1: U1.7 (PC1(PSCIN1/OC1B)); also elsewhere on the board
PC2: U1.10 (PC2(T0/PSCOUT22)); also elsewhere on the board
PC3: U1.11 (PC3(T1/PSCOUT23)); also elsewhere on the board
PC4: U1.21 (PC4(ADC8/AMP1-)); also elsewhere on the board
PC5: U1.22 (PC5(ADC9/AMP1+)); also elsewhere on the board
PC6: R17.1, R18.2, SW1.W (2), U1.26 (PC6(ADC10/ACMP1))
PC7: LCD1.4 (RS), U1.29 (PC7(D2A))
PD0: R22.1, U1.1 (PD0(PSCOUT00/XCK/SS_A))
PD1: C12.1, R27.2, U1.4 (PD1(PSCIN0/CLKO))
PD2: U1.5 (PD2(PSCIN2/OC1A/MISO_A)); also elsewhere on the board
PD3: U1.6 (PD3(TXD/DALI/OC0A/SS/MOSI_A)); also elsewhere on the board
PD4: U1.16 (PD4(ADC1/RXD/DALI/ICP1A/SCK_A)); also elsewhere on the board
PD5: U1.17 (PD5(ADC2/ACMP2)); also elsewhere on the board
PD6: U1.18 (PD6(ADC3/ACMPM/INT0)); also elsewhere on the board
PD7: U1.19 (PD7(ACMP0)); also elsewhere on the board
PE1: U1.14 (PE1(OC0B/XTAL1)); also elsewhere on the board
PE2: U1.15 (PE2(ADC0/XTAL2)); also elsewhere on the board
RESET: R3.2, U1.3 (PE0(RESET/OCD)); also elsewhere on the board

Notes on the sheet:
MCU
Display
Buttons
Beeper

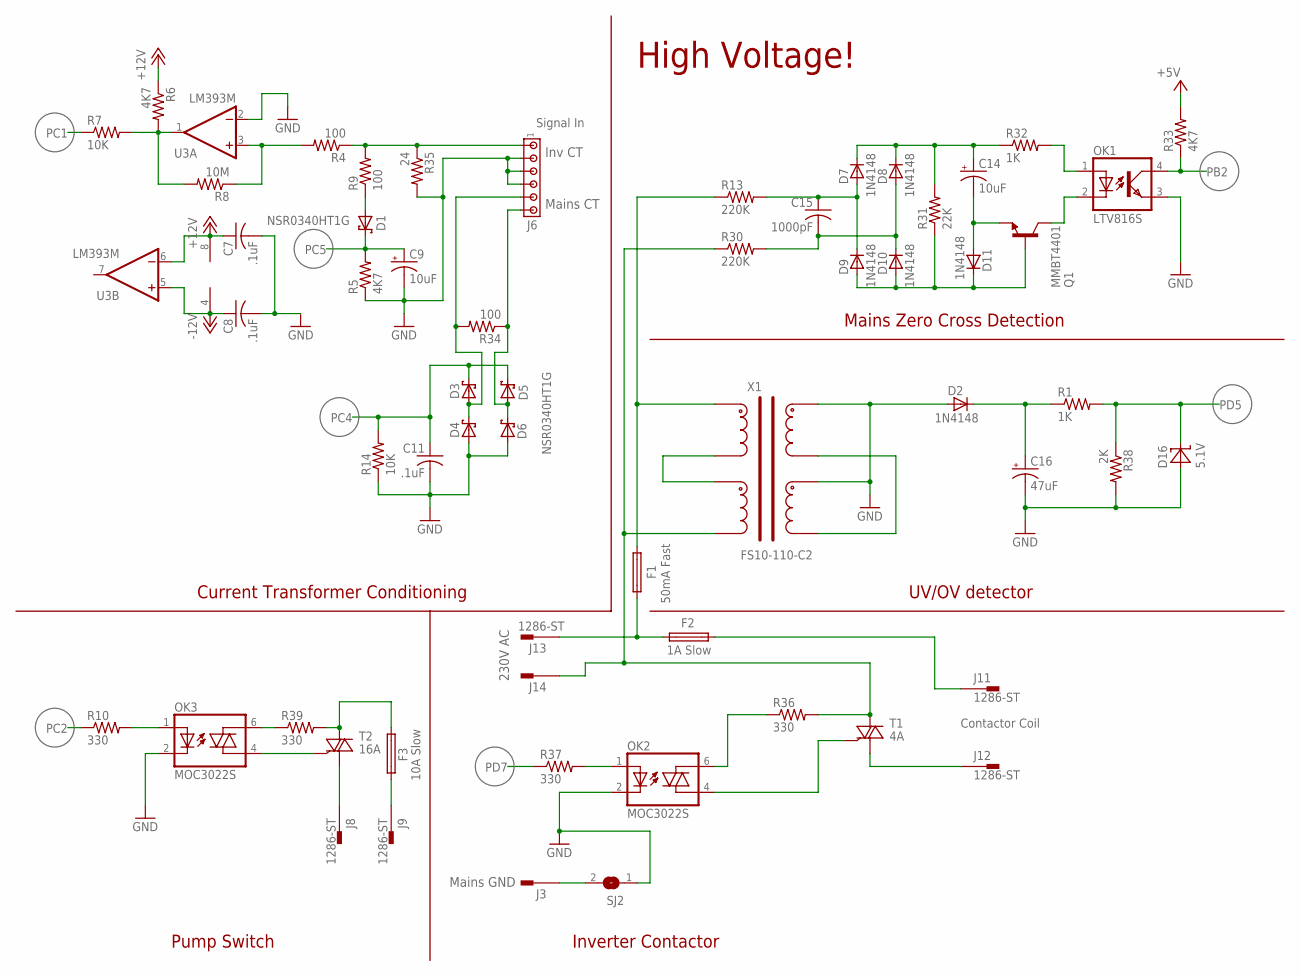
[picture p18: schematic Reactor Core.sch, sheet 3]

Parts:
C7, C8, C11: .1uF; C1206
C9, C14: 10uF; 153CLV-0405
C15: 1000pF; C1206
C16: 47uF; 153CLV-0605
D1, D3, D4, D5, D6: NSR0340HT1G; SOD-323
D2, D7, D8, D9, D10, D11: 1N4148; SOD-123
D16: 5.1V; SOD-323
F1: 50mA Fast; TR5; MPN MRF 50
F2: 1A Slow; FC211-5X20
F3: 10A Slow; FC211-5X20
J3, J8, J9, J11, J12, J13, J14: 1286-ST; 62409-1
J6: Signal In; 10X06MTA
OK1: LTV816S; SMD4
OK2: MOC3022S; 6-SMD
OK3: MOC3022S; 6-SMD; MPN MOC3022S
Q1: MMBT4401; SOT23
R1: 1K; R1206; MPN RNCP1206FTD100R
R4, R9: 100; R1206
R5, R6, R33: 4K7; R1206
R7, R14: 10K; R1206
R8: 10M; R1206
R10: 330; M1206
R13, R30: 220K; R1206
R31: 22K; R1206
R32: 1K; R1206
R34: 100; R1206; MPN RNCP1206FTD100R
R35: 24; R2512; MPN 352124RFT
R36, R37, R39: 330; R1206
R38: 2K; R1206; MPN RNCP1206FTD100R
SJ2: 0; SJ
T1: 4A; DPAK-TRIAC
T2: 16A; DPAK-TRIAC; MPN T1635-700G-TR
U3: LM393M; SO08; MPN LM393M
X1: FS10-110-C2

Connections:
240A: F1.1, F2.1A (1), F2.1B (1), J13.A1, J13.A2
240B: J14.A1, J14.A2, R30.1, R36.2, T1.A2, X1.P$4
+5V: R33.2; also elsewhere on the board
+12V: C7.1, R6.1, U3.6 (-IN), U3.8 (V+); also elsewhere on the board
-12V: C8.1, U3.4 (V-), U3.5 (+IN); also elsewhere on the board
GND: C7.2, C8.2, C9.-, C11.2, C16.-, D2.A, D4.A, D6.A, D16.A, J6.3 (4), J6.4 (3), J6.5 (2), OK1.3 (EMIT), OK2.2 (C), OK3.2 (C), R5.1, R14.1, R35.2, R38.2, SJ2.1, U3.2 (-IN), X1.P$5, X1.P$7; also elsewhere on the board
MGND: J3.A1, J3.A2, SJ2.2
unnamed: OK3.1 (A), R10.2
unnamed: OK3.6 (A2), R39.1
unnamed: OK2.1 (A), R37.2
unnamed: J6.6 (1), R4.1, R9.2, R35.1
unnamed: F3.2A (2), F3.2B (2), R39.2, T2.A2
unnamed: R4.2, R8.1, U3.3 (+IN)
unnamed: OK3.4 (A1), T2.G
unnamed: R6.2, R7.2, R8.2, U3.1 (OUT)
unnamed: D1.A, R9.1
unnamed: D3.A, D4.C, J6.2 (5), R34.2
unnamed: D5.A, D6.C, J6.1 (6), R34.1
unnamed: X1.P$6, X1.P$8
unnamed: X1.P$2, X1.P$3
unnamed: C15.1, D7.A, D9.C, R13.2
unnamed: C15.2, D8.A, D10.C, R30.2
unnamed: OK2.6 (A2), R36.1
unnamed: OK2.4 (A1), T1.G
unnamed: D9.A, D10.A, D11.C, Q1.1 (B), R31.1
unnamed: C14.+, D7.C, D8.C, R31.2, R32.1
unnamed: C14.-, D11.A, Q1.2 (E)
unnamed: J12.A1, J12.A2, T1.A1
unnamed: OK1.1 (A), R32.2
unnamed: OK1.2 (C), Q1.3 (C)
unnamed: F2.2A (2), F2.2B (2), J11.A1, J11.A2
unnamed: J8.A1, J8.A2, T2.A1
unnamed: C16.+, D2.C, R1.1
unnamed: F1.2, R13.1, X1.P$1
unnamed: F3.1A (1), F3.1B (1), J9.A1, J9.A2
PB2: OK1.4 (COL), R33.1; also elsewhere on the board
PC1: R7.1; also elsewhere on the board
PC2: R10.1; also elsewhere on the board
PC4: C11.1, D3.C, D5.C, R14.2; also elsewhere on the board
PC5: C9.+, D1.C, R5.2; also elsewhere on the board
PD5: D16.C, R1.2, R38.1; also elsewhere on the board
PD7: R37.1; also elsewhere on the board

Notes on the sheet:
Inv CT
Mains CT
UV/OV detector
230V AC
Mains Zero Cross Detection
Current Transformer Conditioning
Contactor Coil
Pump Switch
Inverter Contactor
High Voltage!
Mains GND

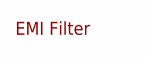
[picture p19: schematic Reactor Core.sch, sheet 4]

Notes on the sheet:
EMI Filter

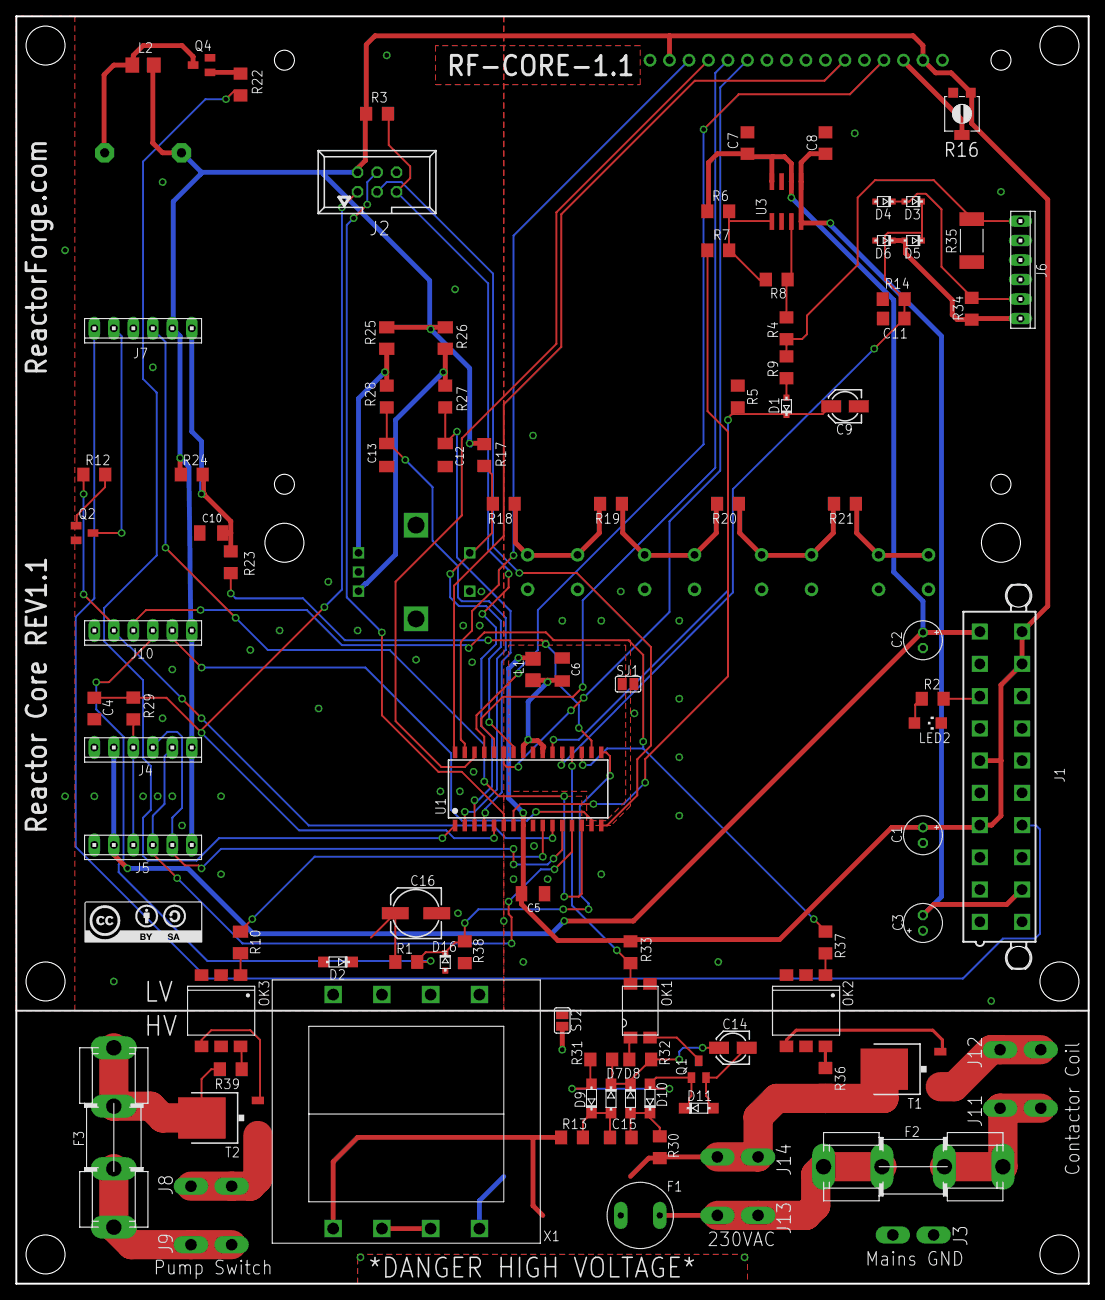
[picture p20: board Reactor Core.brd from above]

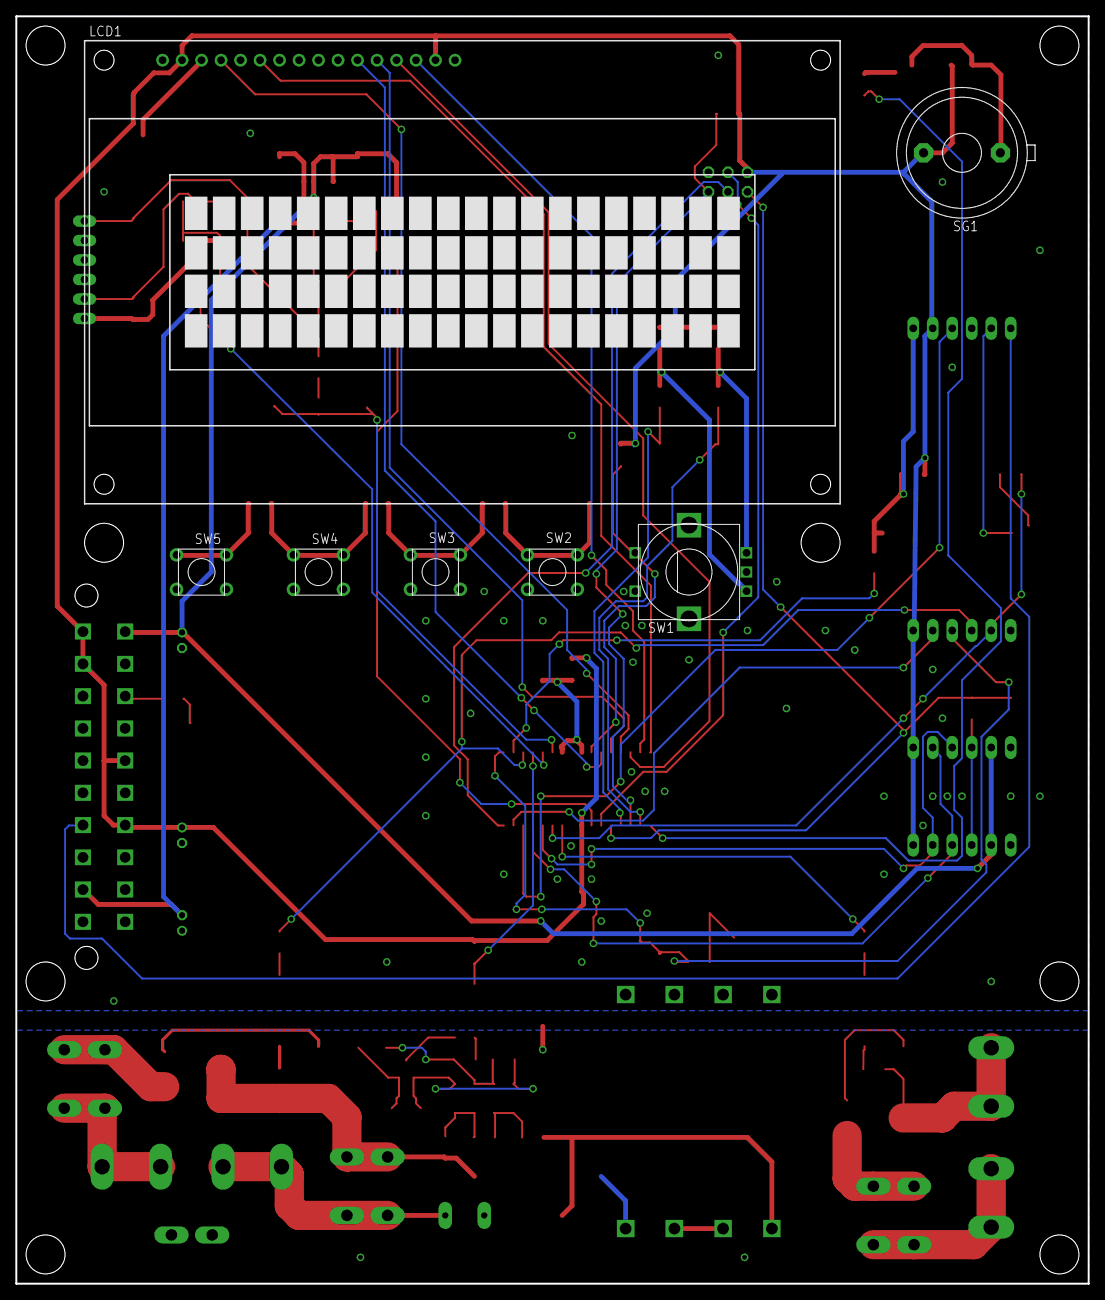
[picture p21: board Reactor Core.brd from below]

Board: 2 copper layers, 139.7 x 165.1 mm, 106 parts (7 on the bottom side), 80 nets.

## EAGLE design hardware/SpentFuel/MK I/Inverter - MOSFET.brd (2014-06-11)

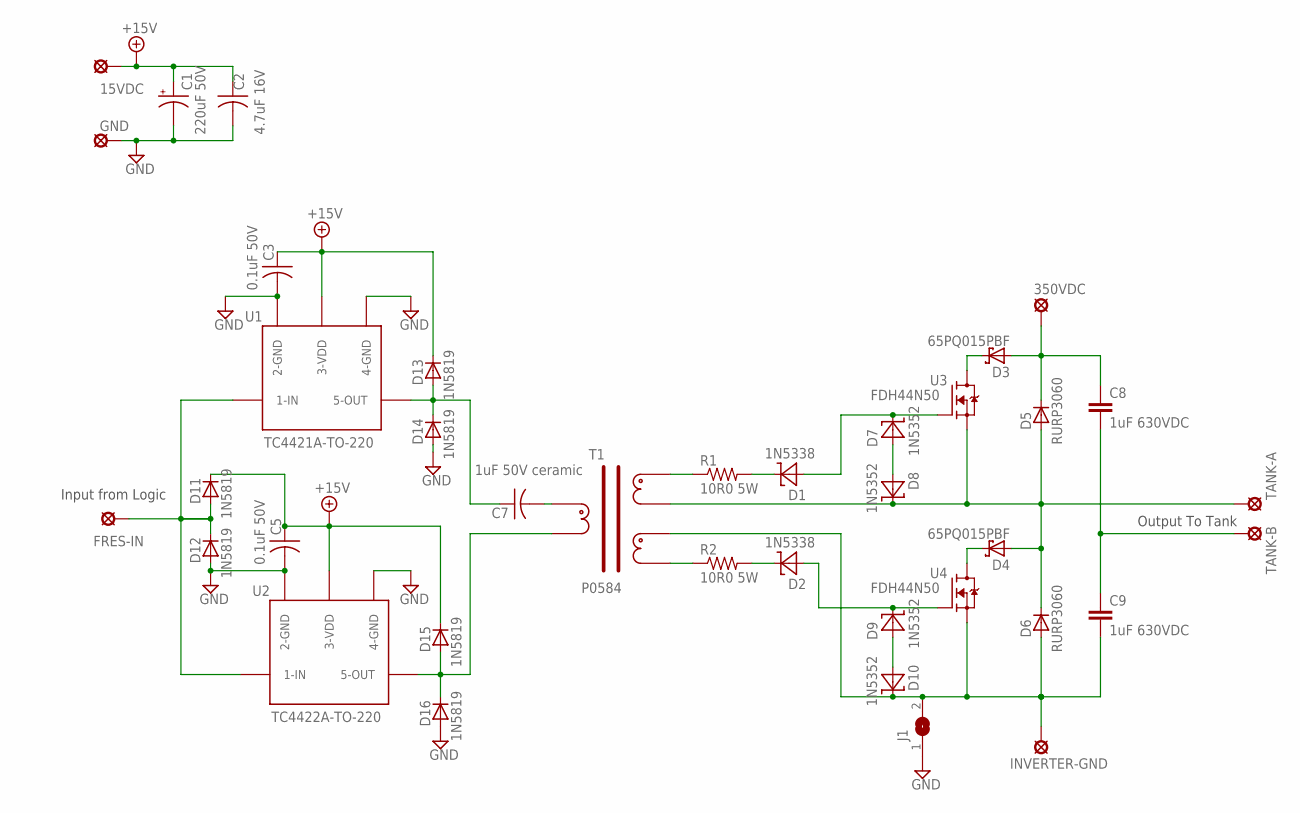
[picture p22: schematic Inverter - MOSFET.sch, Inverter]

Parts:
15VDC, 350VDC: SE14
C1: 220uF 50V; E5-10,5
C2: 4.7uF 16V; C1206
C3, C5: 0.1uF 50V; C1206
C7: 1uF 50V ceramic; C1206
C8, C9: 1uF 630VDC; CAPACITOR2.2-AXIAL
D1, D2: 1N5338; DIODE.4-AXIAL
D3, D4: 65PQ015PBF; TO-247AC-V
D5, D6: RURP3060; TO-220CA2-V
D7, D8, D9, D10: 1N5352; DIODE.4-AXIAL
D11, D12, D13, D14, D15, D16: 1N5819; DIODE.4-AXIAL
FRES-IN: SE14
GND: SE14
INVERTER-GND: SE14
J1: SJW
R1, R2: 10R0 5W; P0817/22
T1: P0584
TANK-A: SE14
TANK-B: SE14
U1: TC4421A-TO-220; TO-220-8TAB-H
U2: TC4422A-TO-220; TO-220-8TAB-H
U3, U4: FDH44N50; TO-247-V

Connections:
350VDC: 350VDC.MP, C8.P$1 (1), D3.1 (A), D3.3 (A), D5.C
+15V: 15VDC.MP, C1.+, C2.1, C3.1, C5.1, D11.C, D13.C, D15.C, U1.3 (3-VDD), U1.TAB (3-VDD), U2.3 (3-VDD), U2.TAB (3-VDD)
GND1: C1.-, C2.2, C3.2, C5.2, D12.A, D14.A, D16.A, GND.MP, J1.1, U1.2 (2-GND), U1.4 (4-GND), U2.2 (2-GND), U2.4 (4-GND)
INVERTER-GND: C9.P$2 (2), D6.A, D10.C, INVERTER-GND.MP, J1.2, T1.P$8, U4.3 (S)
unnamed: D11.A, D12.C, FRES-IN.MP, U1.1 (1-IN), U2.1 (1-IN)
unnamed: C7.1, D13.A, D14.C, U1.5 (5-OUT)
unnamed: C7.2, T1.P$1
unnamed: R1.1, T1.P$3
unnamed: D15.A, D16.C, T1.P$10, U2.5 (5-OUT)
unnamed: R2.1, T1.P$7
unnamed: D1.C, R1.2
unnamed: D2.C, R2.2
unnamed: D3.2 (C), U3.2 (D)
unnamed: D4.2 (C), U4.2 (D)
unnamed: D9.A, D10.A
unnamed: D7.A, D8.A
TANK-A: D4.1 (A), D4.3 (A), D5.A, D6.C, D8.C, T1.P$4, TANK-A.MP, U3.3 (S)
TANK-B: C8.P$2 (2), C9.P$1 (1), TANK-B.MP
U3-GATE: D1.A, D7.C, U3.1 (G)
U4-GATE: D2.A, D9.C, U4.1 (G)

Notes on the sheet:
Output To Tank
Input from Logic

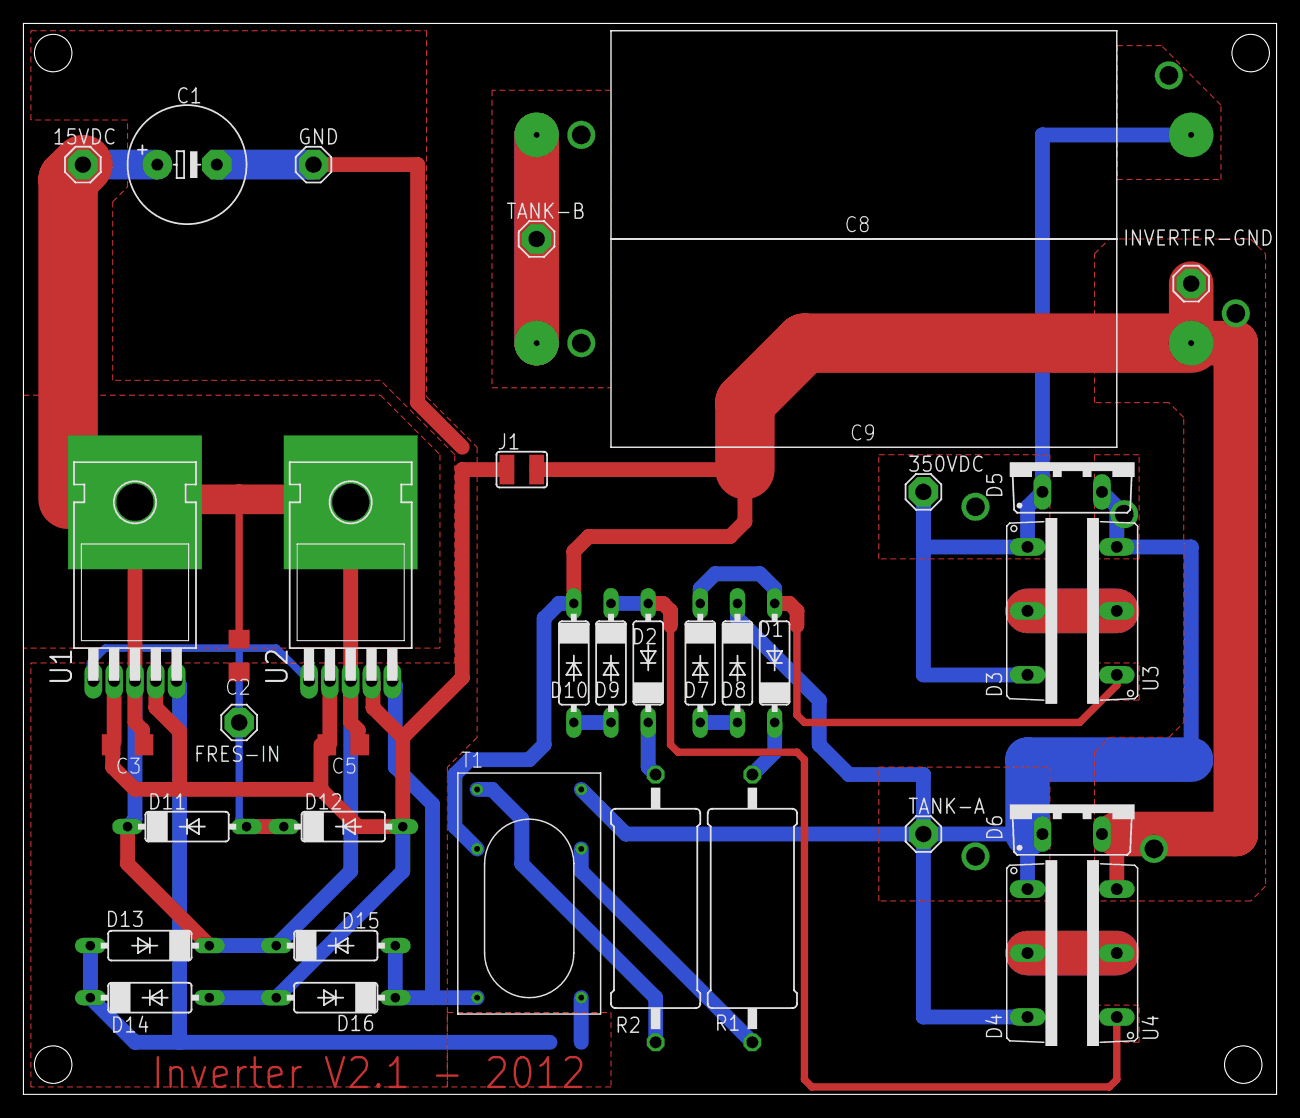
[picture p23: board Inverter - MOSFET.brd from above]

Board: 2 copper layers, 107.0 x 91.4 mm, 38 parts (1 on the bottom side), 20 nets.

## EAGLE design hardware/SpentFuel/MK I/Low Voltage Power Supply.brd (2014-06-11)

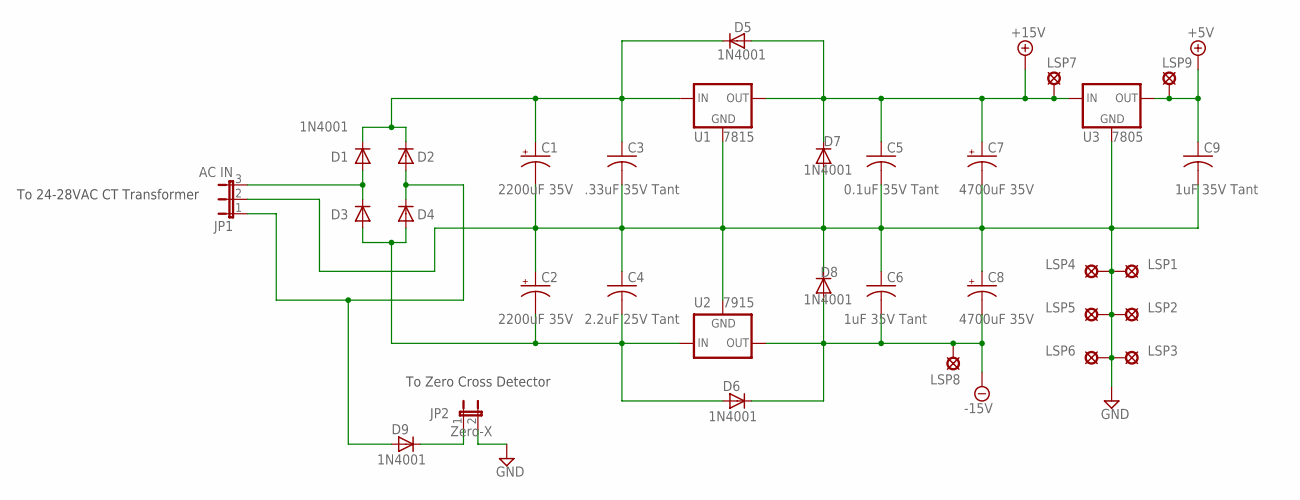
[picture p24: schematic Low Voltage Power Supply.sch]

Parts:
C1, C2: 2200uF 35V; E7,5-18
C3: .33uF 35V Tant; C1206
C4: 2.2uF 25V Tant; C1206
C5: 0.1uF 35V Tant; C1206
C6, C9: 1uF 35V Tant; C1206
C7, C8: 4700uF 35V; E7,5-18
D1, D2, D3, D4, D5, D6, D7, D8, D9: 1N4001; DIODE.4-AXIAL
JP1: AC IN; JP2
JP2: Zero-X; JP1
LSP1, LSP2, LSP3, LSP4, LSP5, LSP6, LSP7, LSP8, LSP9: SE14
U1: 7815; 78XXS
U2: 7915; 79XXS
U3: 7805; 78XXS

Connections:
+5V: C9.1, LSP9.MP, U3.OUT
+15V: C5.1, C7.+, D5.A, D7.C, LSP7.MP, U1.OUT, U3.IN
-15V: C6.2, C8.-, D6.C, D8.A, LSP8.MP, U2.OUT
GND: C1.-, C2.+, C3.2, C4.1, C5.2, C6.1, C7.-, C8.+, C9.2, D7.A, D8.C, JP1.2, JP2.2, LSP1.MP, LSP2.MP, LSP3.MP, LSP4.MP, LSP5.MP, LSP6.MP, U1.GND, U2.GND, U3.GND
unnamed: C1.+, C3.1, D1.C, D2.C, D5.C, U1.IN
unnamed: D2.A, D4.C, D9.A, JP1.1
unnamed: D1.A, D3.C, JP1.3
unnamed: C2.-, C4.2, D3.A, D4.A, D6.A, U2.IN
unnamed: D9.C, JP2.1

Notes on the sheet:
To Zero Cross Detector
To 24-28VAC CT Transformer

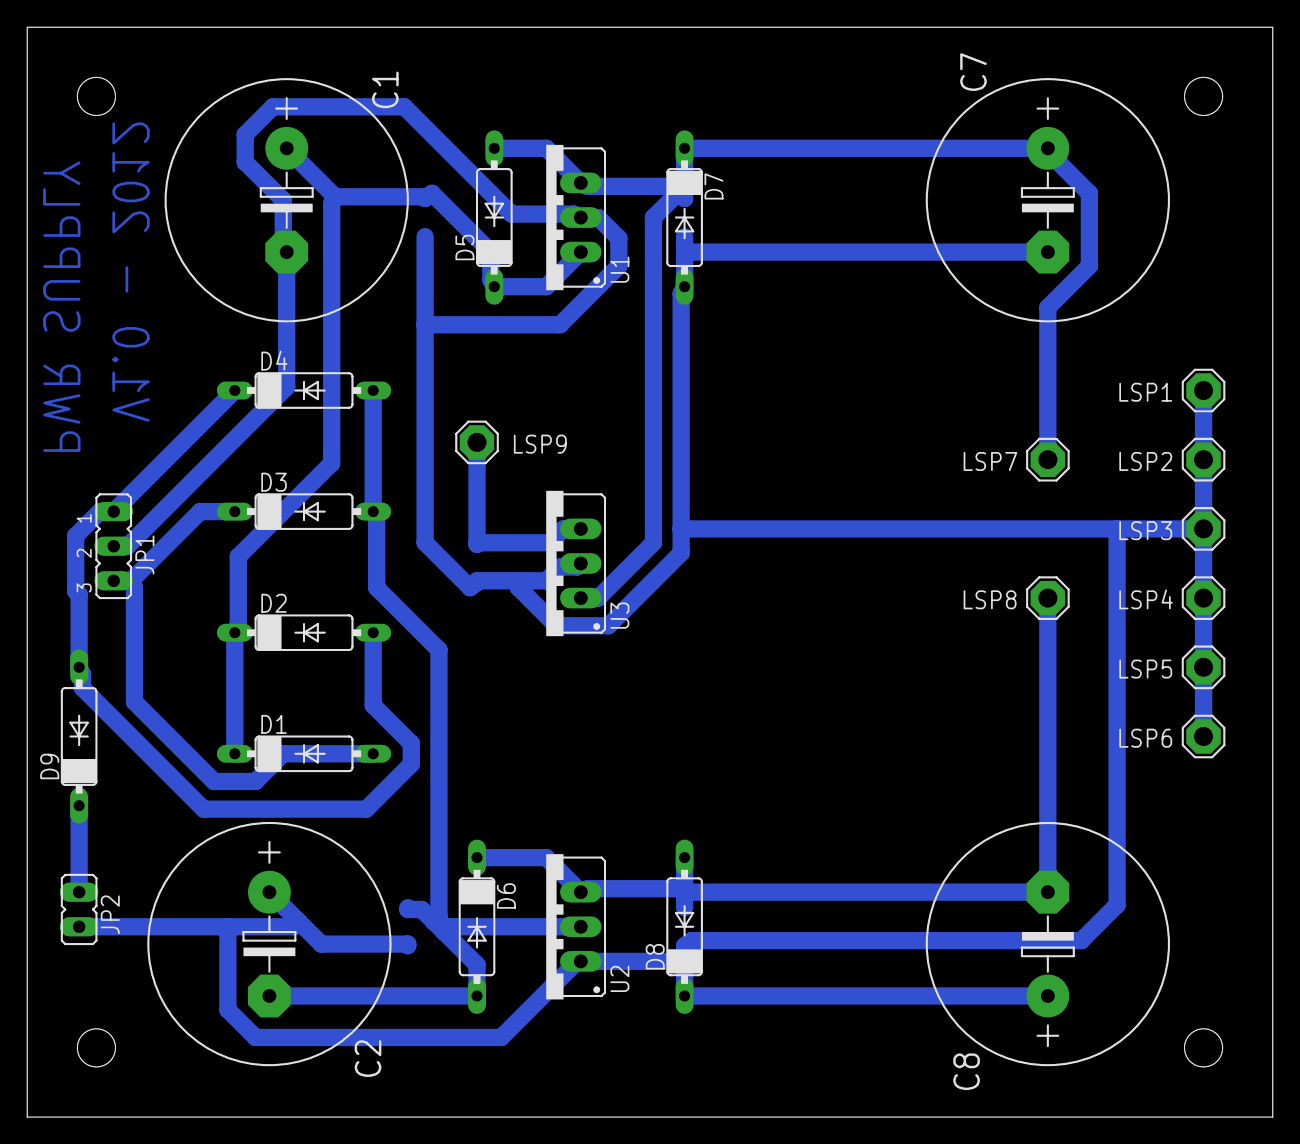
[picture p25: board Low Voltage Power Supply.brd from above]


Board: 2 copper layers, 91.4 x 80.0 mm, 32 parts (5 on the bottom side), 9 nets.

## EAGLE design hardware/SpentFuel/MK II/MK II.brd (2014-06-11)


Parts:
C6: 2.2uF 25V Tant; C1206
C7, C14: 1uF 35V Tant; C1206
C8: .33uF 35V Tant; C1206
C9: 0.1uF 35V Tant; C1206
C10, C11: 2200uF 35V; E7,5-18
C12, C13: 4700uF 35V; E7,5-18
D1, D2, D3, D4, D5, D6, D7, D8: 1N4001; DIODE.4-AXIAL
JP1: AC IN; JP2
TP1_GND, TP2_GND, TP3_+15, TP4_-15V, TP5_5V: SE14
U7: 7815; 78XXS
U8: 7915; 79XXS
U9: 7805; 78XXS

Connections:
+5V: C7.1, TP5_5V.MP, U9.OUT; also elsewhere on the board
+15V: C9.1, C12.+, D5.A, D7.C, TP3_+15.MP, U7.OUT, U9.IN; also elsewhere on the board
-15V: C13.-, C14.2, D6.C, D8.A, TP4_-15V.MP, U8.OUT; also elsewhere on the board
GND: C6.1, C7.2, C8.2, C9.2, C10.-, C11.+, C12.-, C13.+, C14.1, D7.A, D8.C, JP1.2, TP1_GND.MP, TP2_GND.MP, U7.GND, U8.GND, U9.GND; also elsewhere on the board
unnamed: C8.1, C10.+, D1.C, D2.C, D5.C, U7.IN
unnamed: D2.A, D4.C, JP1.1
unnamed: D1.A, D3.C, JP1.3
unnamed: C6.2, C11.-, D3.A, D4.A, D6.A, U8.IN

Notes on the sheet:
24-28VAC


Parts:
C15, C16, C23, C27: 0.1uF; C1206
C17: 100nF; C1206
C18: 1-400pF; C1206
C19, C20: .47uF; C1206
C21, C25: .1uF; C1206
C22: 1uF; C1206
C24: .22uF; C1206
C26: 10uF; E2,5-7
D10, D17, D18: 1N4148; SOD-123
DIS1: NHD-0216K1Z-FS(RGB)-FBW-REV1; TUXGR_16X2_R2
FO: SE14
I-MAINS: SE14
J1, J3: 22-23-2081
J2: 057-010-1
JP3: VCO; JP2
L1: 10uH; L2012C
PC0, PC1: SE14
R2, R9, R23, R26, R27, R28: 10K; M1206
R3: 100; M1206
R4, R21, R22: 100K; M1206
R5: 50K; M1206
R6, R7: 200K; RTRIM4G/J
R8: 10K; RTRIM4G/J
R10, R25: 4R7K; M1206
R11, R15, R19, R20: 1K; M1206
R12, R13, R14, R24: 2K; M1206
R16: 200; M1206
R17, R18: 25K 5W; 0617/22
U10: ATMEGA168A-AU; TQFP32-08
U11: CD4046B; SO16
U12: LM6172; SO08
U13: FOD3180; SO08
U14: MMBT4401; SOT23
X1: CSTCE10M0G55Z; 3-SMD

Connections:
1WIRE: J1.3, R25.2, U10.30 (PD0(RXD))
+5V: C16.2, DIS1.2 (VCC), J1.4, J2.2, L1.1, R2.1, R25.1, U10.4 (VCC), U10.6 (VCC); also elsewhere on the board
+15V: C23.1, C25.1, C27.1, D17.C, R8.1 (E), R26.1, U11.16 (VDD), U12.8 (V+), U13.8; also elsewhere on the board
-15V: C23.2, D10.A, U12.4 (V-); also elsewhere on the board
AVCC: C17.2, L1.2, U10.18 (AVCC), U10.20 (AREF)
FO: FO.MP, U11.3 (CIN), U11.4 (VCOOUT); also elsewhere on the board
GND: C15.2, C16.1, C17.1, C19.2, C20.2, C21.2, C22.2, C24.2, C25.2, C26.+, C27.2, DIS1.1 (GND), DIS1.5 (R/W), J1.6, J2.4, J2.6, J2.8, J2.10, R3.1, R6.1 (E), R7.1 (E), R8.3 (A), R9.1, R15.2, R18.1, R19.1, R22.2, R27.1, U10.3 (GND), U10.5 (GND), U10.21 (GND), U11.8 (VSS), U13.3, U13.5, U14.2 (E), X1.2; also elsewhere on the board
GND1: C22.1, C26.-, R16.2, U10.19 (ADC6)
unnamed: D10.C, D17.A, R28.1, U12.3 (+IN)
unnamed: U12.6 (-IN), U12.7 (OUT)
unnamed: D18.A, J1.5
unnamed: U10.8 (PB7(XTAL2/TOSC2)), X1.1
unnamed: U10.7 (PB6(XTAL1/TOSC1)), X1.3
unnamed: J2.5, R2.2, U10.29 (PC6(/RESET))
unnamed: DIS1.3 (CONTR), R3.2
unnamed: R11.1, U13.2
unnamed: DIS1.4 (RS), U10.9 (PD5(T1))
unnamed: DIS1.6 (E), U10.10 (PD6(AIN0))
unnamed: DIS1.11 (D4), U10.11 (PD7(AIN1))
unnamed: DIS1.12 (D5), U10.14 (PB2(SS/OC1B))
unnamed: DIS1.13 (D6), J2.1, U10.15 (PB3(MOSI/OC2))
unnamed: DIS1.14 (D7), J2.9, U10.16 (PB4(MISO))
unnamed: C18.1, U11.6 (CX)
unnamed: C18.2, U11.7 (CX)
unnamed: R4.1, R6.2 (S)
unnamed: R5.1, R7.2 (S)
unnamed: R4.2, U11.11 (R1)
unnamed: R5.2, U11.12 (R2)
unnamed: JP3.3, R8.2 (S)
unnamed: R19.2, R21.1, U12.2 (-IN)
unnamed: R26.2, U11.5 (INH), U14.3 (C)
unnamed: R10.2, U10.12 (PB0(ICP))
unnamed: R11.2, U10.13 (PB1(OC1A))
unnamed: R9.2, R10.1, U14.1 (B)
unnamed: R14.2, U11.2 (PC1)
unnamed: R12.2, U13.6, U13.7
unnamed: C15.1, R14.1, R15.1, R16.1
unnamed: C19.1, R12.1, R13.2
unnamed: C20.1, JP3.1, R13.1
unnamed: C21.1, JP3.2, U11.9 (VCOIN)
unnamed: R27.2, U12.5 (+IN)
unnamed: R20.1, R21.2, U12.1 (OUT)
unnamed: R20.2, U11.14 (SIGIN)
unnamed: R17.1, R28.2
unnamed: J1.8, R18.2
unnamed: C24.1, R23.1, R24.2
unnamed: D18.C, R22.1, R24.1
unnamed: I-MAINS.MP, R23.2, U10.22 (ADC7)
unnamed: J1.7, R17.2
unnamed: J2.7, U10.17 (PB5(SCK))
unnamed: J3.8, U10.2 (PD4(XCK/T0))
unnamed: J3.7, U10.1 (PD3(INT1))
unnamed: J3.6, U10.32 (PD2(INT0))
unnamed: J3.5, U10.31 (PD1(TXD))
unnamed: J3.4, U10.28 (PC5(ADC5/SCL))
unnamed: J3.3, U10.27 (PC4(ADC4/SDA))
unnamed: J3.2, U10.26 (PC3(ADC3))
unnamed: J3.1, U10.25 (PC2(ADC2))
unnamed: PC0.MP, U10.23 (PC0(ADC0))
unnamed: PC1.MP, U10.24 (PC1(ADC1))

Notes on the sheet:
To Inverter


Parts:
C1: 47uF; E2,5-7
C2, C4: 0.1uF; C1206
C3: 22uF; C1206
C5: 1uF 50V; C1206
D11, D12, D13, D14, D15, D16: 1N5819-SOD-123; SOD-123
J1: 22-23-2081
R1: 2R2; 0207/10
T1: P0585
U1: TC4421A-SOIC-8; SOIC-8
U2: TC4422A-SOIC-8; SOIC-8
U3, U4, U5, U6: FQPF20N06L; TO-220-V

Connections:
+15V: C1.+, C2.1, C4.1, D11.C, D13.C, D15.C, U1.P$1 (1-VDD), U1.P$8 (8-VDD), U2.P$1 (1-VDD), U2.P$8 (8-VDD), U4.2 (D), U6.2 (D); also elsewhere on the board
FO: D11.A, D12.C, U1.P$2 (2-IN), U2.P$2 (2-IN); also elsewhere on the board
GND: C1.-, C2.2, C4.2, D12.A, D14.A, D16.A, T1.P$4, T1.P$6, U1.P$4 (4-GND), U1.P$5 (5-GND), U2.P$4 (4-GND), U2.P$5 (5-GND), U3.3 (S), U5.3 (S); also elsewhere on the board
unnamed: J1.2, T1.P$9, U3.2 (D), U4.3 (S)
unnamed: C5.1, D13.A, D14.C, U1.P$6 (6-OUT), U1.P$7 (7-OUT)
unnamed: C5.2, T1.P$1
unnamed: R1.2, T1.P$10
unnamed: D15.A, D16.C, R1.1, U2.P$6 (6-OUT), U2.P$7 (7-OUT)
unnamed: C3.1, T1.P$3, U5.2 (D), U6.3 (S)
unnamed: T1.P$2, U6.1 (G)
unnamed: T1.P$5, U5.1 (G)
unnamed: T1.P$8, U4.1 (G)
unnamed: T1.P$7, U3.1 (G)
unnamed: C3.2, J1.1

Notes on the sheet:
Input from Logic
IGBT1 G1
IGBT1 E1
IGBT1 E2
IGBT1 G2
IGBT2 G1
IGBT2 E1
IGBT2 E2
IGBT2 G2



Board: 2 copper layers, 161.3 x 100.0 mm, 104 parts (5 on the bottom side), 75 nets.

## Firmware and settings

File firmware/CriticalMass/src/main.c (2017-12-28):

/*
 * File:      main.c
 * Title      ReactorForge - CriticalMass
 * Hardware:  ReactorCore AT90PWM316
 * Author:    Josh Campbell
 * Created:   8/24/2013
 * Modified:  12/22/2017
 * Version:   0.0.a1
 * Link:      https://github.com/ThingEngineer/ReactorForge
 * Website:   https://reactorforge.com
 * This work is licensed under a Creative Commons Attribution-ShareAlike 4.0 International License.
 * License:		https://reactorforge.com/licence/
 *
 * DESCRIPTION
 *        The ReactorForge project is an open source hardware platform for
 *        high power induction heating, designed for heavy use and reliable
 *        performance in real-world applications.
 *
 * Coding Standards:
 *        WIP - These standards are not yet fully implemented.
 *        http://ieng9.ucsd.edu/~cs30x/indhill-cstyle.html
 *        https://users.ece.cmu.edu/~eno/coding/CCodingStandard.html
 *

 *
 * THIS CODE AND ASSOCIATED DOCUMENTATION (THE "SOFTWARE") IS PROVIDED "AS IS",
 * WITHOUT WARRANTY OF ANY KIND, EXPRESS OR IMPLIED, INCLUDING BUT NOT LIMITED
 * TO THE WARRANTIES OF MERCHANTABILITY, FITNESS FOR A PARTICULAR PURPOSE AND
 * NONINFRINGEMENT. IN NO EVENT SHALL THE AUTHORS OR COPYRIGHT HOLDERS BE LIABLE
 * FOR ANY CLAIM, DAMAGES OR OTHER LIABILITY, WHETHER IN AN ACTION OF CONTRACT,
 * TORT OR OTHERWISE, ARISING FROM, OUT OF OR IN CONNECTION WITH THE SOFTWARE OR
 * THE USE OR OTHER DEALINGS IN THE SOFTWARE.
 */


#include <main.h>


/****************************************************************************
* Setup
****************************************************************************/
void setup() {
  //Set port data direction registers and pull ups
	DDRB = 0b00000000;
	DDRD = 0b10000000;
	DDRC = 0b00001100;
	DDRE = 0b00000000;

	// Initial output port states
	bit_clear(INDICATOR_PORT, BIT(INDICATOR_BIT));// Turn indicator light off
	bit_clear(CONTACTOR_PORT, BIT(CONTACTOR_BIT));// Turn contactor off
	bit_clear(PUMP_PORT, BIT(PUMP_BIT));					// Turn pump switch off
	bit_clear(BUZZER_PORT, BIT(BUZZER_BIT));			// Turn buzzer off

	// Set pull ups
	bit_set(IGBT_FAULT_PORT, BIT(IGBT_FAULT_BIT));// IGBT Fault

	// USART Setup
	bit_set(UCSRB, BIT(RXEN) | BIT(TXEN));				// Enable receiver and transmitter
	bit_set(UCSRC, BIT(UCSZ0) | BIT(UCSZ1));			// Use 8-bit character sizes
	UBRRH = (BAUD_PRESCALE >> 8);									// Load upper 8-bits of the baud rate value into the high byte of the UBRR register
	UBRRL = BAUD_PRESCALE;												// Load lower 8-bits of the baud rate value into the low byte of the UBRR register
	stdout = &uart_output;												// Redirect STDOUT to UART
	stdin  = &uart_input;													// Redirect STDIN to UART

	// Power Stage Controller Setup
	bit_set(PSOC0,  BIT(POEN0A));									// PSC 0 Synchronization and Output Configuration - Enable Part A - Buzzer output
	//bit_set(PSOC1,  BIT());											// PSC 1 Synchronization and Output Configuration
	bit_set(PSOC2, BIT(POEN2B) | BIT(POEN2A));		// PSC 2 Synchronization and Output Configuration - Enable Part A & B - Inverter output

	bit_set(PCNF0, BIT(POP0));										// PSC 0 Configuration Register - 1 ramp mode, Active high
	bit_set(PCNF1, BIT(PCLKSEL1));								// PSC 1 Configuration Register - 1 ramp mode, fast clock
	bit_set(PCNF2, BIT(PCLKSEL2));								// PSC 2 Configuration Register - 1 ramp mode, fast clock

	bit_set(PCTL0, BIT(PPRE00));									// PSC 0 Control Register - /4 Prescaler
	//bit_set(PCTL1, BIT());											// PSC 1 Control Register
	bit_set(PCTL2, BIT(PARUN2));									// PSC 2 Control Register - Autostart PSC2 with PSC1

	//bit_set(PFRC0A, BIT());											// PSC 0 Input A Control Register - Enable capture, on PSCIN0, falling edge trigger, noise canceler off, no action only used for resonant inverter phase detection by reading input capture register
	//bit_set(PFRC0B, BIT());											// PSC 0 Input B Control Register
	bit_set(PFRC1A, BIT(PCAE0A));									// PSC 1 Input A Control Register - Enable capture, on PSCIN0, falling edge trigger, noise canceler off, no action only used for resonant inverter phase detection by reading input capture register
	//bit_set(PFRC1B, BIT());											// PSC 1 Input B Control Register
	bit_set(PFRC2A, BIT(PCAE2A) | BIT(PRFM2A2) | BIT(PRFM2A1) | BIT(PRFM2A0));	// PSC 2 Input A Control Register - Enable capture, on PSCIN2, low level trigger, mode 7 (halt)
	//bit_set(PFRC2B, BIT());											// PSC 2 Input B Control Register

	//bit_set(PIM0, BIT(PEVE0A));									// PSC 0 Interrupt Mask Register - Enable interrupt on block A capture event
	//bit_set(PIM1, BIT(PEVE1A));									// PSC 1 Interrupt Mask Register - Enable interrupt on block A capture event
	//bit_set(PIM2, BIT(PEVE2A));									// PSC 2 Interrupt Mask Register - Enable interrupt on block A capture event

	// Analog Comparator Setup
	//bit_set(AC0CON, BIT(AC0EN));								// ACMP0
	//bit_set(DIDR1, BIT(ACMP0D));								// Digital Input Disable for ACMP0

	// ADC Setup
	bit_set(ADMUX, BIT(MUX3) | BIT(MUX2) | BIT(MUX1) | BIT(MUX0));		// ADC Multiplexer Register (V ref on AREF, right adjust, Ground ADC input)
	bit_set(ADCSRA, BIT(ADEN) | BIT(ADSC) | BIT(ADPS2));							// ADC Control and Status Register A (Enable ADC, Start ADC (initialize), Prescaler 16)
	bit_set(ADCSRB, BIT(ADHSM));																			// ADC Control and Status Register B (High Speed Mode)
	bit_set(DIDR0, BIT(ADC2D));																				// Digital Input Disable Register 0
	bit_set(DIDR1, BIT(ADC8D) | BIT(ADC9D) | BIT(ADC10D));						// Digital Input Disable Register 1

	// LCD Setup
	lcd_init(LCD_DISP_ON);							// Initialize LCD
	lcd_clrscr();												// Clear LCD display

	// OneWire setup
	OW_nSensors = search_sensors();			// Scan One Wire for devices

	// INT1 Interrupt - AC Mains ZCD
  bit_set(EICRA, BIT(ISC11));					// INT1 Falling edge trigger
  bit_set(EIMSK, BIT(INT1));					// Enable INT1

	// INT3 Interrupt - Rotary encoder B output
	bit_set(EICRA, BIT(ISC31));					// INT3 Falling edge trigger
	bit_set(EIMSK, BIT(INT3));					// Enable INT3

	// Timer1 Interrupt - AC mains phase synchronization angle timer
	bit_set(TCCR1A, BIT(WGM12));				// Timer1 CTC Mode
	bit_set(TIMSK1, BIT(OCIE1A));				// Enable CTC Interrupt

	sei();															// Enable Global Interrupt

	inverter_current_max = 200;					// Initial maximum inverter current

	Kp = 1;
	Ki = 1;
	Kd = 0;

	phase_offset = 140;
}

/****************************************************************************
* MAIN
****************************************************************************/
int main(void)
{
	// Run setup code
	setup();
	// Reset system settings
	reset_ss();

	// Write startup screen
	lcd_gotoxy(0,0);
	lcd_puts("  ReactorForge.com");
	lcd_gotoxy(0,1);
	lcd_puts("  Core Ver 0.0a1");
	lcd_gotoxy(0,3);
	lcd_puts("    Select Mode");

	// Wait for button press to select mode
	lcd_key = btnNONE;
	while(lcd_key == btnNONE)
	{
		// Read buttons and save current state
		lcd_key = read_buttons();
	}

	// Clear LCD
	lcd_clrscr();

	// Turn contactor on
	bit_set(CONTACTOR_PORT, BIT(CONTACTOR_BIT));

	//#########################################################################################
	if (lcd_key == btn1)	// Enter manual control mode if button 1 is held during startup
	{
		//puts("Test Mode");
		lcd_clrscr();
		lcd_puts("Manual Control Mode");
		// ***Test Control***
		while(1)
		{
			lcd_key = read_buttons();

			if (lcd_key == 4)
			{
				_delay_ms(1000);
				lcd_key = read_buttons();
				if (lcd_key == 4) bit_flip(CONTACTOR_PORT, BIT(CONTACTOR_BIT));
			}

			if (bit_is_clear(SS_SW_PIN, SS_SW_BIT))
			{
				if (running_flag == 0)
				{
					reset_ss();
					start_psc();
					lcd_clrscr();
					bit_set(EIMSK, BIT(INT1));	// Enable INT1
					bit_set(INDICATOR_PORT, BIT(INDICATOR_BIT));	// Indicator on
				}
			}
			else
			{
				if (running_flag == 1)
				{
					stop_psc(0);
					lcd_clrscr();
					lcd_puts_P("Manual Control Mode");
					bit_clear(INDICATOR_PORT, BIT(INDICATOR_BIT));	// Indicator off
					bit_clear(PCTL0, BIT(PRUN0));		// Stop buzzer
				}
			}

// 			if (lcd_key == btn1)
// 			{
// 				if (running_flag == 0)
// 				{
// 					reset_ss();
// 					start_psc();
//
// 					lcd_clrscr();
// 					bit_set(EIMSK, BIT(INT1));	// Enable INT1
// 				}
// 				else
// 				{
// 					stop_psc(0);
//
// 					lcd_clrscr();
// 					lcd_puts_P("Test Mode");
// 					//puts("Test Mode");
// 				}
//
// 				_delay_ms(250);
// 			}

			if (enc > enc_prev)
			{
				decr_freq();
			}
			if (enc < enc_prev)
			{
				incr_freq(1);
			}
			enc_prev = enc;

			if (lcd_key == btn2)
			{
				incr_freq(1);
				_delay_ms(10);
			}

			if (lcd_key == btn1)
			{
				decr_freq();
				_delay_ms(10);
			}

// 			if (lcd_key == btn3)
// 			{
// 				decr_freq();
//
// 				//incr_duty_cycle(5);
//
// //  				deadtime = deadtime + 1;
// //  				set_frequency();
// //  				_delay_ms(250);
//  			}
//
// 			if (lcd_key == btn4)
// 			{
// 				incr_freq(1);
//
// 				//decr_duty_cycle(5);
//
// //  				deadtime = deadtime - 1;
// //  				set_frequency();
// //  				_delay_ms(250);
// 			}

			if (running_flag == 0) control_loop++;
			if ( (running_flag == 0) & (control_loop == 5) )
			{
				control_loop = 0;
				lcd_gotoxy(0,1);
				if ( DS18X20_start_meas( DS18X20_POWER_EXTERN, NULL ) == DS18X20_OK)
				{
					_delay_ms( DS18B20_TCONV_12BIT );
					for ( i = 0; i < OW_nSensors; i++ )
					{
						if ( DS18X20_read_decicelsius( &gSensorIDs[i][0], &deciCelsius ) == DS18X20_OK )
						{
							if (i == 2) lcd_gotoxy(0,2);
							if (i == 0) lcd_puts("Out ");
							if (i == 1) lcd_puts("Inv ");
							if (i == 2) lcd_puts("Amb ");
							if (i == 3) lcd_puts("In  ");

							char str[5];
							deciCelsius = ((18 * (deciCelsius / 10) + 32 * 10) + 5);
							DS18X20_format_from_decicelsius( deciCelsius , str, 10 );
							//itoa(deciCelsius, str, 10);
							lcd_puts(str);
							lcd_puts(" ");
						}
					}
				}
			}

			if (running_flag == 0)
			{
				if (enc > enc_prev) phase_offset++;
				if (enc < enc_prev) phase_offset--;
				enc_prev = enc;

				char str[5];					// Buffer for the ASCII string
				lcd_gotoxy(0,3);
				itoa(phase_offset, str, 10);
				lcd_puts(str);
				lcd_puts("  ");
			}

			if ( (running_flag == 1) & (ac_peak == 1) )
			{
				ac_peak = 0;

				phase_current = (PICR1 & 0x0FFF) - phase_offset;
				//phase_delta = phase_previous - phase_current;
				phase_delta = abs(phase_previous - phase_current);

				if (phase_delta < 100)
				{
					phase_average = ( ( (filter_level - 1) * phase_average) + phase_current) / filter_level;	// Moving average filter
					error_current = ( ( ( (filter_level - 1) * error_current) + abs(phase_average - ontime) ) / filter_level );
				}

				//setpoint = (phase_current - phase_offset);

				// Get ADC Values
				inverter_current = get_adc(9);
				mains_current = get_adc(8);

				inverter_current_avg = ( ( (filter_level - 1) * inverter_current_avg) + inverter_current) / filter_level;
				mains_current_avg = ( ( (filter_level - 1) * mains_current_avg) + mains_current) / filter_level;

				if (bit_is_set(PIFR2, PEV2A))						// If IGBT hardware fault has been detected on PSCIN2 via external event A interrupt flag register
				{
					stop_psc(igbt_fault);
				}

// 				if (lock_flag = 0)
// 				{
// 					if (phase_average > ontime) decr_freq();
// 					if (phase_average < ontime) lock_flag = 1;
// 				}
// 				if (lock_flag = 1)
// 				{
// 					if ((phase_average - (phase_deadband * 1)) > ontime) decr_freq();
// 					if ((phase_average + (phase_deadband * 1)) < ontime) incr_freq(1);
// 				}



				if (control_loop == 0 || control_loop == 5)
				{
					print_buf[0] = start_code;
					print_buf[1] = 0;//setpoint;
					print_buf[2] = ontime;
					print_buf[3] = phase_current;
					print_buf[4] = phase_average;
					print_buf[5] = phase_adjustment;
					print_buf[6] = error_current;
					print_buf[7] = inverter_current_max;
					print_buf[8] = inverter_current_avg;
					print_buf[9] = mains_current_avg;

					for (i = 0; i < 10; i++)
					{
						uart_print16( print_buf[i] );
					}

					char str[5];					// Buffer for the ASCII string
					//lcd_clrscr();
					lcd_home();
					itoa(inverter_current, str, 10);
					lcd_puts(str);
					lcd_puts(" ");
					itoa(mains_current, str, 10);
					lcd_puts(str);
					lcd_puts("   ");

// 					lcd_gotoxy(0,1);
// 					itoa(ontime, str, 10);
// 					lcd_puts(str);
// 					lcd_puts(" ");
// 					itoa(setpoint, str, 10);
// 					lcd_puts(str);
// 					lcd_puts(" ");
// 					itoa(phase_current, str, 10);
// 					lcd_puts(str);
// 					lcd_puts("   ");

// 					lcd_gotoxy(0,3);
// 					itoa(lcd_key, str, 10);   // convert integer into string (decimal format)
// 					lcd_puts(str);

					lcd_gotoxy(0,1);
				}

				if (control_loop == 1)
				{
					DS18X20_start_meas( DS18X20_POWER_EXTERN, NULL );

					control_loop2++;
					if (control_loop2 == 10)
					{
						control_loop2 = 0;
						bit_set(PCTL0, BIT(PRUN0));		// Buzzer on
					}
				}

				if ( (control_loop >= 6) & (control_loop <=9) )
				{
					i = control_loop - 6;

					if ( DS18X20_read_decicelsius( &gSensorIDs[i][0], &deciCelsius ) == DS18X20_OK )
					{
						//uart_print16( deciCelsius );

						if (i == 2) lcd_gotoxy(0,2);
						if (i == 0) lcd_puts("Out ");
						if (i == 1) lcd_puts("Inv ");
						if (i == 2) lcd_puts("Amb ");
						if (i == 3) lcd_puts("In  ");

						char str[5];
						deciCelsius = ((18 * (deciCelsius / 10) + 32 * 10) + 5);
						DS18X20_format_from_decicelsius( deciCelsius , str, 10 );
						lcd_puts(str);
						lcd_puts(" ");
					}

// 					if ( DS18X20_start_meas( DS18X20_POWER_EXTERN, NULL ) == DS18X20_OK)
// 					{
// 						//if (OW_nSensors == 0)
// 						//{
// 						//	lcd_puts("No sensors found");
// 						//}
// 						//_delay_ms( DS18B20_TCONV_12BIT );
// 						for ( i = 0; i < OW_nSensors; i++ )
// 						{
// 							if ( DS18X20_read_decicelsius( &gSensorIDs[i][0], &deciCelsius ) == DS18X20_OK )
// 							{
// 								uart_print16( deciCelsius );
// 								if (i == 2) lcd_gotoxy(0,2);
//
// 								char str[5];
// 								DS18X20_format_from_decicelsius( deciCelsius, str, 10 );
// 								lcd_puts(str);
// 								lcd_puts(" ");
//
// 								//fahrenheit = (deciCelsius * 9.0)/ 5.0 + 32.0;
// 								//fahrenheit = (18*(deciCelsius)+(10*16*32))/16;
// 								//DS18X20_format_from_decicelsius( fahrenheit, s, 10 );
//
// 							}
// 							//else
// 							//{
// 							//	lcd_puts( "CRC Error" );
// 							//	OW_error++;
// 							//}
// 						}
// 					}
				}

				control_loop++;
				if (control_loop == 10)
				{
					control_loop = 0;
					//bit_flip(INDICATOR_PORT, BIT(INDICATOR_BIT));
					bit_clear(PCTL0, BIT(PRUN0));		// Buzzer off
				}

				phase_previous = phase_current;

				bit_set(EIMSK, BIT(INT1));	// Enable INT1

			}

		}
		// ***END Test Control***
	}

	//#########################################################################################
	//#########################################################################################
	//if (lcd_key == btnRIGHT)	// Enter manual control mode if button 2 is held during startup
	//{
		//puts("Ready");
		//_delay_ms(500);
		lcd_puts("Ready");

		while(1)
		{
			lcd_key = read_buttons();

			if (bit_is_clear(SS_SW_PIN, SS_SW_BIT))
			{
				if (running_flag == 0)
				{
					reset_ss();
					start_psc();
					lcd_clrscr();
					bit_set(EIMSK, BIT(INT1));	// Enable INT1
					bit_set(INDICATOR_PORT, BIT(INDICATOR_BIT));	// Indicator on
				}
			}
			else
			{
				if (running_flag == 1)
				{
					stop_psc(0);
					lcd_clrscr();
					lcd_puts_P("Ready");
					bit_clear(INDICATOR_PORT, BIT(INDICATOR_BIT));	// Indicator off
					bit_clear(PCTL0, BIT(PRUN0));		// Stop buzzer
				}
			}

			if (running_flag == 1)
			{
				if (enc < enc_prev)
				{
					if (inverter_current_max > 14)
					{
						inverter_current_max -= 5;
					}
				}
				if (enc > enc_prev)
				{
					inverter_current_max += 5;
					if (inverter_current_max > 1024)
					{
						inverter_current_max = 1024;
					}
				}
				enc_prev = enc;

// 				if (lcd_key == btn3)
// 				{
// 					inverter_current_max = inverter_current_max + 5;
// 					if (inverter_current_max > 1024)
// 					{
// 						inverter_current_max = 1024;
// 					}
// 					//Ki++;
// 				}
//
// 				if (lcd_key == btn2)
// 				{
// 					if (inverter_current_max > 14)
// 					{
// 						inverter_current_max = inverter_current_max - 5;
// 					}
// 					//Ki--;
// 					//if (Ki < 0) Ki = 0;
// 				}

	// 			if (lcd_key == btn4)
	// 			{
	// 				//setpoint++;
	// 				//phase_adjustment++;
	// 				Kp++;
	// 			}
	//
	// 			if (lcd_key == btn3)
	// 			{
	// 				//setpoint--;
	// 				//phase_adjustment--;
	// 				Kp--;
	// 				if (Kp < 1) Kp = 1;
	// 			}
			}

			if (running_flag == 0)
			{
				if (enc > enc_prev) phase_offset++;
				if (enc < enc_prev) phase_offset--;
				enc_prev = enc;

				char str[5];					// Buffer for the ASCII string
				lcd_gotoxy(0,1);
				itoa(phase_offset, str, 10);
				lcd_puts(str);
				lcd_puts("  ");
			}

			if ( (running_flag == 1) & (ac_peak == 1) )
			{
				//bit_set(PORTE, BIT(1));
				ac_peak = 0;

				phase_current = (PICR1 & 0x0FFF);					// Get the value from the last PSC0 capture event (Mask out upper 4 bits) - represents phase offset between inverter voltage and inverter current
				phase_delta = abs(phase_previous - phase_current);

				if (phase_delta < 100)
				{
					phase_average = ( ( (filter_level - 1) * phase_average) + phase_current) / filter_level;	// Moving average filter
				}

				// Get ADC Values
				inverter_current = get_adc(9);
				mains_current = get_adc(8);
				//mains_current = ( ( 1 * mains_current) + get_adc(3)) / 2; // test filter on mains current

				// Calculate resonant phase errors
				//error_current = phase_current - setpoint;
				//error_current = abs(setpoint - ontime);
				error_current = ( ( ( (filter_level - 1) * error_current) + abs(setpoint - ontime) ) / filter_level );
				error_delta = abs(error_current - error_previous);	// Save error delta between current and previous error
				error_previous = error_current;						// Save current error to previous error before next control loop iteration

				// ***Halt condition checks***
				if (bit_is_set(PIFR2, PEV2A))						// If IGBT hardware fault has been detected on PSCIN2 via external event A interrupt flag register
				{
					stop_psc(igbt_fault);
				}

// 	 			if ((ontime == ontime_ceiling) & (first_pass == 1))						// If ontime ceiling is reached then halt
// 				{
// 	 				//error_status = ceiling_reached;
// 	 				stop_psc(ceiling_reached);
// 	 			}

	 			if (ontime == ontime_floor)							// If ontime floor is reached then halt
				{
	 				//error_status = floor_reached;
	 				stop_psc(floor_reached);
	 			}

				if ((scan_period == 0) & (lock_flag == 0))			// If no lock has occurred in the alloted time
				{
					//error_status = scan_timeout;
					stop_psc(scan_timeout);
				}

// 				if (lock_flag == 1)
// 				{
// 	//  				if (inverter_current > (inverter_current_max + 200))	// If instantaneous inverter current spikes above maximum allowed after resonant lock
// 	// 				{
// 	// 					//error_status = inverter_current_spike;
// 	// 					stop_psc(inverter_current_spike);
// 	// 				}
//
// 					if (phase_delta > delta_max)
// 					{
// 						//error_status = phase_delta_max;
// 						stop_psc((phase_delta_max));
// 					}
//
// 					if (phase_delta < delta_min)
// 					{
// 						//error_status = phase_delta_min;
// 						stop_psc((phase_delta_min));
// 					}
//
// 					if (upper_limit_cnt == upper_limit_hits)		// If the upper limit has been hit over the Upper_limit_hits setting then halt
// 					{
// 						//error_status = upper_soft_limit;
// 						stop_psc(upper_soft_limit);
// 					}
//
// 					if (lower_limit_cnt == lower_limit_hits)		// If the lower limit has been hit over the Lower_limit_hits setting then halt
// 					{
// 						//error_status = lower_soft_limit;
// 						stop_psc(lower_soft_limit);
// 					}
// 				}
				// ***END Halt condition checks***


				// Resonant lock detection
				//if ((phase_current == setpoint) & (error_current < phase_deadband) & (abs(phase_delta) < 5) & (error_current < setpoint) & (error_current > 0) & (first_pass == 1) & (lock_flag == 0))	//Resonance has been achieved, set flag and lock value
				//if ((phase_current == setpoint) & (first_pass == 1) & (lock_flag == 0))	//Resonance has been achieved, set flag and lock value
				if ( (error_current < (phase_deadband * 2)) & (error_delta < 3) & (first_pass == 1) & (lock_flag == 0) & (ontime >= setpoint - phase_deadband) )
				{
					lock_flag = 1;
					lock_value = ontime;
				}

				//Proportional control for resonant tank frequency to regulate maximum inverter current
	 			//if (lock_flag == 1)
	 			//{
// 	 				if (mains_current > inverter_current_max)
// 	 				{
// 	 					phase_adjustment = phase_adjustment + 2;
//
// 						if ( (mains_current - inverter_current_max) > 200)
// 						{
// 							phase_adjustment = phase_adjustment + 10;
// 						}
// 	 				}
//
// 	 				if (((mains_current + 25) < inverter_current_max) & phase_adjustment > 0)
// 	 				{
// 	 					phase_adjustment = phase_adjustment - 1;
// 	 				}

	  				//phase_adjustment = (inverter_current - inverter_current_max) + phase_adjustment;
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

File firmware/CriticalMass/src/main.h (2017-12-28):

/*
 * main.h
 *
 * Created: 12/16/2017
 * Author: Josh Campbell
 */


#ifndef MAIN_H
#define MAIN_H

#if (__GNUC__ * 100 + __GNUC_MINOR__) < 303
#error "AVR-GCC 3.3 or later is required, update AVR-GCC compiler!"
#endif

#include <stdlib.h>
#include <avr/io.h>
#include <avr/interrupt.h>
#include <util/delay.h>
#include <avr/sfr_defs.h>
#include <avr/eeprom.h>
#include <string.h>
#include <stdio.h>

#include <lcd.h>
#include <ds18x20.h>
#include <onewire.h>


#define USART_BAUDRATE 57600
#define BAUD_PRESCALE (((F_CPU / (USART_BAUDRATE * 16UL))) - 1)
#define NEWLINESTR "\r"

#define MAXSENSORS 4


/****************************************************************************
* Function prototypes
****************************************************************************/
void init(void);

void reset_ss(void);
void start_psc(void);
void stop_psc(uint8_t);
void incr_freq(uint8_t);
void decr_freq(void);
void set_frequency(void);
uint16_t get_adc(uint8_t);

static void uart_print8(uint8_t val);
static void uart_print16(uint16_t val);
static int uart_putchar(char c, FILE *stream);
static int uart_getchar(FILE *stream);

static uint8_t search_sensors(void);
static uint8_t gSensorIDs[MAXSENSORS][OW_ROMCODE_SIZE];

int read_buttons(void);

// int button0_is_pressed(void);
// int button1_is_pressed(void);
// int button2_is_pressed(void);
// int button3_is_pressed(void);
// int button4_is_pressed(void);


/****************************************************************************
* Macros
****************************************************************************/
#define bit_get(p,m) ((p) & (m))
#define bit_set(p,m) ((p) |= (m))
#define bit_clear(p,m) ((p) &= ~(m))
#define bit_flip(p,m) ((p) ^= (m))
#define bit_write(c,p,m) (c ? bit_set(p,m) : bit_clear(p,m))
#define BIT(x)	(0x01 << (x))									// Converts a bit number into a byte value.
#define LONGBIT(x) ((unsigned long)0x00000001 << (x))
#define BIT_VAL(x,y) (((x) >> (y)) & 1)

static FILE uart_output = FDEV_SETUP_STREAM(uart_putchar, NULL, _FDEV_SETUP_WRITE);	// SDOUT buffer
static FILE uart_input = FDEV_SETUP_STREAM(NULL, uart_getchar, _FDEV_SETUP_READ);		// SDIN buffer
//FILE uart_io FDEV_SETUP_STREAM(uart_putchar, uart_getchar, _FDEV_SETUP_RW);	// One buffer which works for both SDIN and SDOUT.

// Store string in PROGMEM rather than loading into RAM at program start
#define F(string_literal) (reinterpret_cast<const __FlashStringHelper *>(PSTR(string_literal)))


/****************************************************************************
* Port aliases
****************************************************************************/
// Start/Stop switch
#define SS_SW_PORT PORTD
#define SS_SW_PIN PIND
#define SS_SW_BIT 6

// IGBT Fault - Triggers PSCIN2
#define IGBT_FAULT_PORT PORTD
#define IGBT_FAULT_PIN PIND
#define IGBT_FAULT_BIT 2

// Encoder output A - Determines directoin
#define ENC_A_PORT PORTD
#define ENC_A_PIN PIND
#define ENC_A_BIT 1

// Encoder output B - Triggers INT3_vect
#define ENC_B_PORT PORTC
#define ENC_B_PIN PINC
#define ENC_B_BIT 0

// Indicator output
#define INDICATOR_PORT PORTC
#define INDICATOR_BIT 3

// Mains Contactor Coil output
#define CONTACTOR_PORT PORTD
#define CONTACTOR_BIT 7

// Pump switch output
#define PUMP_PORT PORTC
#define PUMP_BIT 2

// Buzzer
#define BUZZER_PORT PORTD
#define BUZZER_PIN PIND
#define BUZZER_BIT 0

#define DEBOUNCE_TIME 25			// Time to wait while "de-bouncing" button
#define LOCK_INPUT_TIME 200			// Time to wait after a button press


/****************************************************************************
* Variable and constant declarations
****************************************************************************/
typedef struct
{
	unsigned char bit0:1;
	unsigned char bit1:1;
	unsigned char bit2:1;
	unsigned char bit3:1;
	unsigned char bit4:1;
	unsigned char bit5:1;
	unsigned char bit6:1;
	unsigned char bit7:1;
}io_reg;

static volatile uint16_t mains_current;		// Mains current ADC value
//static volatile uint16_t tank_voltage;		// Tank voltage ADC value
static volatile uint16_t inverter_current;	// Inverter current ADC value
uint16_t mains_current_avg;
uint16_t inverter_current_avg;

uint16_t inverter_current_max;		// Maximum inverter current

// Buck converter variables
// uint16_t dc_ontime;				// Base PWM frequency
// uint8_t dc_deadtime;				// PWM deadtime
// uint16_t dc_max_duty_cycle;		// Maximum PWM duty cycle (max DC output)
// uint16_t dc_min_duty_cycle;		// Minimum PWM duty cycle (min DC output)
// uint16_t dc_duty_cycle_on;		// The portion of dc_ontime that should be on per cycle
// uint16_t dc_duty_cycle_off;		// The portion of dc_ontime that should be off per cycle
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

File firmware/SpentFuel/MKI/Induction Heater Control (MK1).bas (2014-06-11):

'*******************************************************************************
'        I²Reactor
'        Induction Heater Control - Resonant PLL Fo lock w/current limit
'        Ver 1.0
'        07/2012
'****************************** Chip Settings **********************************
'$regfile = "m168def.dat"
$regfile = "4433def.dat"
$crystal = 10000000
'$baud = 9600
'$prog &HFF , &HF7 , &HCC , &HF9                             ' Fuse bytes
'
'****************************** Port Settup ************************************
Config Portb = &B00111111                                   ' Config I/O ports 1=output (PORTB.1 is PWM output OC1A)
Config Portc = Input
Config Portd = &B11110000
'Didr0 = &B00111111                                          ' Disable the digital input buffer on all ADC ports (PORTC)

Vco_enable Alias Portb.0                                    ' VCO enable/disable - Active high (Low disables)
Reset Vco_enable                                            ' Ensure VCO is disabled

Sw1 Alias Pinc.2                                            ' Switch ports (Active low)
Sw2 Alias Pinc.3
Sw3 Alias Pinc.4
Sw4 Alias Pinc.5
Sw5 Alias Pind.1
Set Portc.2                                                 ' Set pull-ups
Set Portc.3
Set Portc.4
Set Portc.5
Set Portd.1

Led Alias Portd.4
'
'********************************** LCD Setup **********************************
Config Lcdpin = Pin , Db4 = Portd.7 , Db5 = Portb.2 , Db6 = Portb.3 , Db7 = Portb.4 , E = Portd.6 , Rs = Portd.5
Config Lcd = 16 * 1a
Initlcd

Deflcdchar [0] , 24 , 4 , 8 , 28 , 32 , 32 , 32 , 32        ' Squared ^2
'Deflcdchar 1 , 4 , 4 , 4 , 4 , 21 , 14 , 4 , 32             ' Down arrow
'Deflcdchar 2 , 32 , 4 , 2 , 31 , 2 , 4 , 32 , 32            ' Holding arrow ->
'Deflcdchar 3 , 4 , 14 , 21 , 4 , 4 , 4 , 4 , 32             ' Up arrow
Cursor Off Noblink
Cls
'
'****************************** Program Variables ******************************
Dim Desired_phase As Word                                   ' Desired phase offset
Dim Phase(5) As Word                                        ' Phase buffer    ' Reduced from 25 to 5 for 4433, was working really well on 25
Dim Phase_avg As Long                                       ' Running average phase reading

'Dim Desired_current As Word                                 ' Desired current value
'Dim Current(7) As Word                                      ' Current buffer
'Dim Current_avg As Long                                     ' Running average current
'Dim Current_diff As Word                                    ' Delta between average and desired current
Dim Over_current As Bit                                     ' Over current flag 1=Over current limit
Dim Current_offset As Word

Dim Running_flag As Bit                                     ' 1=VCO is enabled and IH is running, 0=VCO is disabled and IH is in standby
Dim Loop_count As Byte                                      ' Temporary loop counter
Dim Samples As Byte                                         ' Sample counter
Dim Display_delay As Word                                   ' Display delay counter
'
'******************************** Interrupts ***********************************
Config Adc = Single , Prescaler = Auto , Reference = Off

Config Timer1 = Pwm , Pwm = 10 , Compare A Pwm = Clear Up , Compare B Pwm = Disconnect , Prescale = 1
Pwm1a = 1023                                                ' 0 = 0% duty cycle (off) : 1023 = 100% duty cycle on (Start at max VCO Fo, pwm=1023) - Output on PORTB.1

'Config Timer0 = Timer , Prescale = 8
'On Ovf0 Tmr0_isr
'Enable Timer0

Config Int0 = Low Level                                     ' Over current trigger
On Int0 Int0_isr
Enable Int0

Enable Interrupts
'
'******************************* Main Program **********************************
Lcd "I" + Chr(0) + "Reactor Ready"
Desired_phase = 670                                         ' ORG=630
'Desired_current = 200
Phase_avg = 0
'Current_avg = 0

Over_current = 0
Current_offset = 0

Display_delay = 0
Samples = 1
Running_flag = 0
Reset Led                                                   ' LED off
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

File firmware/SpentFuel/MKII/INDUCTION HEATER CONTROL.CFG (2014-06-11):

[COMPILER-CHIP]
Chip=m168def.dat
XRAM=0
Waitstate=0
XA=0
Stacksize=40
Framesize=32
Sstack=16
[COMPILER-OUTPUT]
Report vars=0
Optimize=1
Binary File=1
Hexadecimal File=1
Report File=1
Debug File=1
Error File=1
ASM File=0
LST File=0
OBJ File=1
SWAP File=0
[COMPILER-COMMUNICATION]
Baudrate=9600
Frequency=10000000
[COMPILER-I2C]
Scl=0
Sda=0
[COMPILER-LCD]
DB7=PORTB.7
DB6=PORTB.6
DB5=PORTB.5
DB4=PORTB.4
E=PORTB.3
RS=PORTB.2
LCD=1
BUS mode=0
DATA mode=0
LCD address=C000
LCD-RS=8000
[COMPILER-MISC]
Size Warning=0
1wire=PORTB.0
[COMPILER-SPI]
HW SPI=1
SPICLOCK=13
SPISS=13
SPIMOSI=14
SPIMISO=15

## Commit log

2014-06-07 add photo of beta assembly
2014-06-11 update assembly photo
2014-06-11 Add MKI schematic and board files
    [120V Inverter Power Supply.sch, Inverter - IGBT.sch, Inverter - MOSFET.brd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]
2014-06-11 Add MKII schematic and board files
    [MK II.brd, MK II.sch]
2014-06-11 removed space from directory name
    [120V Inverter Power Supply.sch, Inverter - IGBT.sch, Inverter - MOSFET.brd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]
2014-06-11 add MKII code
    [INDUCTION HEATER CONTROL.CFG]
2014-06-14 added MKII control upgrade board image
2014-06-15 add Hybrid Driver files
    [Hybrid Driver 1.1.brd, Hybrid Driver.brd, Hybrid Driver.sch]
2014-06-16 add hybrid driver connections
2014-06-16 add and update driver images
2015-02-06 Added parts list/BOM
2017-11-16 CriticalMass ReactorForge Core
    Initial Github commit for this schematic and board file
    [Reactor Core.brd, Reactor Core.sch]
2017-11-16 Added .OLD to file names to prevent Github from saying this repository is of the VisualBasic language
    [Induction Heater Control (MK1).bas, Induction Heater Control_M48 (MKII).bas]
2017-12-15 add fuses to ini
2017-12-15 Custom AT90PWM316 board manifest for platformio
2017-12-15 moved platformio board manifest to project scope
2017-12-15 removed f_cpu from board manifest
2017-12-15 changed boad name in board manifest
2017-12-15 vendor name tweak in board manifest
2017-12-15 corrected flash size in board manifest
2017-12-15 changed fuse bytes in board manifest to chip defaults
2017-12-15 added custom script in platformio.ini to set fuse bytes
2017-12-15 revert old BASCOM basic firmware files back to original file names
    [Induction Heater Control (MK1).bas, Induction Heater Control_M48 (MKII).bas]
2017-12-15 custom fuses commented out while testing platform
2017-12-17 removed .platformio/boards, using project level board manifest
2017-12-17 updated project level board manifest, removed lock fuse and corrected default lfuse
2017-12-17 added another fuse calculator
2017-12-17 removed extra_script, did not work for programing fuses, using upload_flags
2017-12-17 moved fuse flags to platformio.ini
2017-12-17 refined fuse comments
2017-12-21 added fuse bit to preserve EEPROM through chip erase
2017-12-22 fixed main header types
    [main.h]
2017-12-23 format correction on fuse comments
2017-12-23 added f_cpu back to the board manafest so platformIO shows cpu speed correctly in the Board Explorer
2017-12-24 removed local board manafest, support merged with platform-atmelavr 1.8.1
2017-12-27 debuging serial device selection
2017-12-28 removed Start/Stop switch & indicator light test code
2017-12-28 removed button press adc value readout test code
2017-12-28 removed contactor/pump switch test code
2017-12-28 removed additional button testing code
2017-12-28 removed temperature sensor test code
2017-12-28 removed Multiplexed buttons pull up, using external hardware pullup
2017-12-28 added missing setup() comments
    [main.c]
2017-12-28 added alias for encoder output B
2017-12-28 removed internal encoder pull ups, they have external pull ups
2017-12-28 removed start/stop switch pull up, it has an external pull ups
2017-12-28 IGBT_FAULT_PIN has a pull up on the driver board, leave soft pull up for better noise immunity
2017-12-31 removed old board version copy
    [Hybrid Driver 1.1.brd]
2017-12-31 reduced board width to 2 inches, added decoupling cap on 5V supply, updated documentation and library components
    [Hybrid Driver.brd, Hybrid Driver.sch]
2017-12-31 updated BOM
2017-12-31 added OSH logo, tweaked silkscreen
    [Hybrid Driver.brd, Hybrid Driver.sch]
2018-01-10 moved OSH logo down, added board renderings
    [Hybrid Driver.brd]
2018-01-11 convert OSH logo text to vector
    [Hybrid Driver.brd, Hybrid Driver.sch]
2018-01-11 silk screen placment tweaks
    [Hybrid Driver.brd]
2018-01-11 increase G1 & G2 net width to 0.032
    [Hybrid Driver.brd]
2018-01-11 more small silk screen placment tweaks
    [Hybrid Driver.brd]
2018-01-12 added BOM with details, links, and pricing
    [BOM_hybrid_driver_v1.3_single_pricing.xlsx]
2018-01-13 added 0 ohm jumper
    [BOM_hybrid_driver_v1.3_single_pricing.xlsx]
2018-09-26 add BOM, Schematic, and Layout
2018-09-26 update filenames
    [Hybrid Driver.sch]

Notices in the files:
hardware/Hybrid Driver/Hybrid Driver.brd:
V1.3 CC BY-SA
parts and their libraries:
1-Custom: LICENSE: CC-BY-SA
